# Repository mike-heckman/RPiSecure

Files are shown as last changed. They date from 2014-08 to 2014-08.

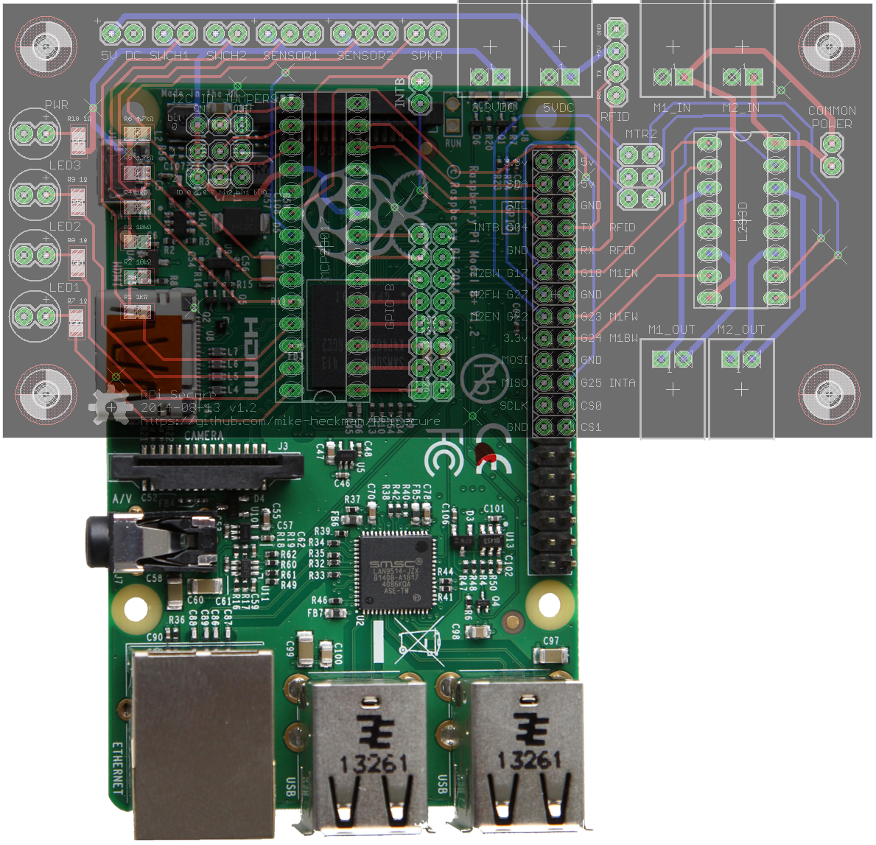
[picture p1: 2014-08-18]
images/Relationship_Pi.png

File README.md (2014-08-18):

Welcome!

This board is designed to "glue" parts to a Raspberry Pi for an RFID door lock.

It attaches on top of the the Pi using the stacking header and uses an L293D
half-H motor driver and an MCP23017 digital IO expander so the other (optional)
components don't take up all the Raspbery Pi's GPIO pins.

If the board is fully populated, it provides the following:

   Two bi-directional motor drivers with either coupled or independent power.
   Connections for two switches, intended for door position (hall-effect sensor) and deadbolt position (tactile momentary switch depressed by the deadbolt).
   Connections for one or two DHT-22 temperature and humidity sensors.
   Connections for up to four LEDs (one is hardwired for power, the other three are on IO ports).
   A connection for a speaker.
   8 additional IO ports addressed through the MCP23017.

The board is designed to use the minimum number of pins on the Raspberry Pi.
To use the second motor driver you have to jumper the MTR2 pins, or tie them
to other pins on the Raspberry Pi breakout.

Also the INTB pins can be jumpered if you want interrupt access to the second
bank of GPIO on the MCP23017 - you don't have to unless you want the interrupt
to go to GPIO pin 4.

You also need to set three jumpers for the MCP23017 3 low id bits.

The board intentionally doesn't draw power from the Pi as it will be powered by
DC/DC power converters from a common 12v source.  There's a pin header near the
upper left corner that provides a +5V and GND power to optionally power the Pi.

The board should work for either the model B or B+ Raspberry Pis.

Datasheets are available for most parts:

L293D Motor Driver:  http://www.farnell.com/datasheets/1804890.pdf
MCP21037 Digital IO: http://www.farnell.com/datasheets/12179.pdf

Standard Traces are 10 mil with 12 mil isolation, the traces for the motor
power in out and to the L293D are larger as it can switch motors up to 36V.
The top and bottom ground planes have been maximized around the chips to allow
them to sink heat into the board.

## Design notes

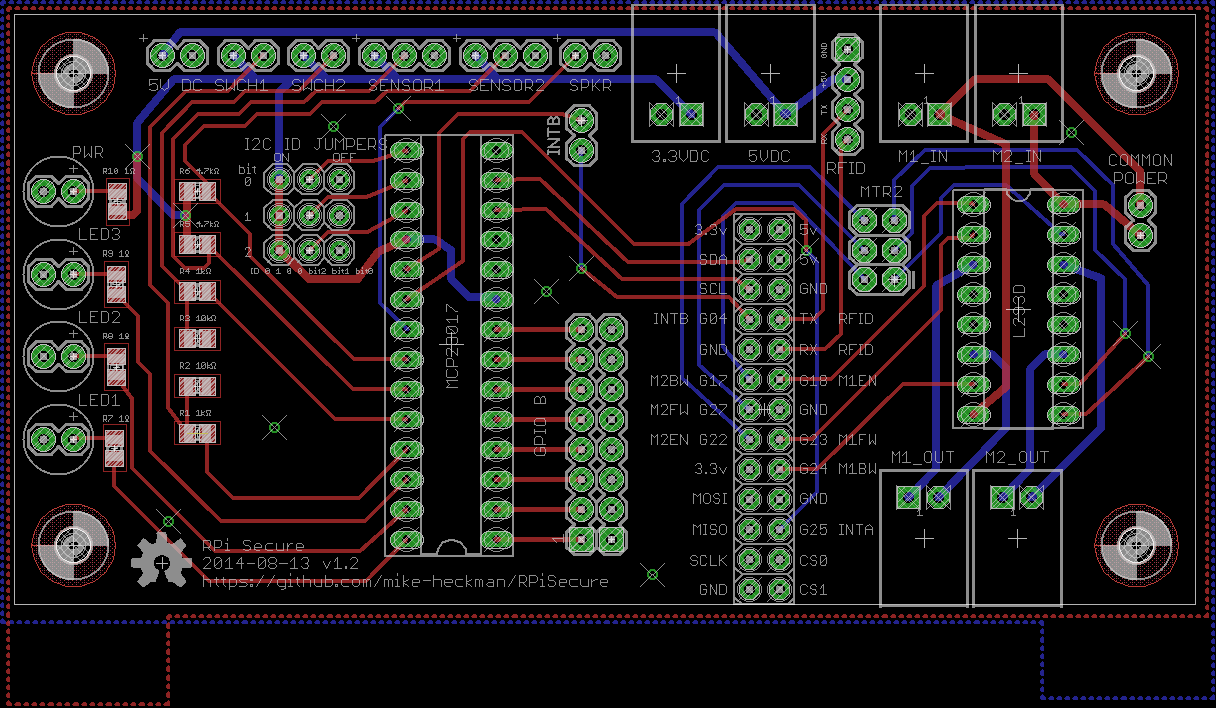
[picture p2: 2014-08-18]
images/RPi_Secure_V1_2.png

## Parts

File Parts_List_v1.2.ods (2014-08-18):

Quantity | Description | Jameco |  | Mouser |  | Adafruit |  | Digikey |  | Newark |  | BEST | Total | Running | Jameco | Mouser | Adafruit | Digikey | Newark | Jameco | Mouser | Adafruit | Digikey | Newark | Total | Order
1 | Industrial & ASIC | link (http://www.jameco.com/webapp/wcs/stores/servlet/Product_10001_10001_1341966_-1) | $2.95 | link (http://www.mouser.com/ProductDetail/Texas-Instruments/L293DNE/?qs=sGAEpiMZZMtYFXwiBRPs0wSafWlCmJbc) | $3.75 | link (http://www.adafruit.com/products/807) | $2.50 | link (http://www.digikey.com/product-search/en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) | $3.75 | link (http://www.newark.com/texas-instruments/l293ne/ic-motor-driver-half-h-1a-dip/dp/06F9524) | $2.24 | $2.24 | $2.24 | $2.24 |  |  |  | $3.75 | $2.24 |  |  |  |  | $2.24 | $2.24 | N01
1 | IC, I/O EXPANDER, 16BIT, 1.7MHZ, DIP-28 |  |  | link (http://www.mouser.com/ProductDetail/Microchip-Technology/MCP23017-E-SP/?qs=sGAEpiMZZMtLck3p7ZBovcWu3APnHHes) | $1.26 | link (http://www.adafruit.com/search?q=MCP23017) | $2.95 | link (http://www.digikey.com/product-detail/en/MCP23017-E/SP/MCP23017-E/SP-ND/894272) | $1.44 | link (http://www.newark.com/microchip/mcp23017-e-sp/ic-i-o-expander-16bit-1-7mhz-dip/dp/31K2959?ost=MCP23017-E/SP) | $1.20 | $1.20 | $1.20 | $3.44 |  |  |  | $1.44 | $1.20 |  |  |  |  | $1.20 | $3.44 | N07
1 | Stacking Header for Raspberry Pi |  |  |  |  | link (http://www.adafruit.com/products/1112) | $1.95 |  |  | link (http://www.newark.com/adafruit-industries/1112/stacking-header-raspberry-pi/dp/53W5726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) | $1.95 | $1.95 | $1.95 | $5.39 |  |  |  |  | $1.95 |  |  |  |  | $1.95 | $5.39 | N09
1 | 16 PIN DIL IC SOCKET (2x8) | link (http://www.jameco.com/webapp/wcs/stores/servlet/Product_10001_10001_37372_-1) | $0.12 | link (http://www.mouser.com/ProductDetail/Microchip-Technology/MCP23017-E-SP/?qs=sGAEpiMZZMtLck3p7ZBovcWu3APnHHes) | $0.10 |  |  | link (http://www.digikey.com/product-detail/en/DILB16P-223TLF/609-4713-ND/4292068) | $0.28 | link (http://www.newark.com/multicomp-formerly-from-spc/spc15498/dip-socket-16pos-through-hole/dp/82K7788) | $0.18 | $0.18 | $0.18 | $5.57 |  |  |  | $0.28 | $0.18 |  |  |  |  | $0.18 | $5.57 | N02
1 | 28 PIN DIL IC SOCKET (2x14) | link (http://www.jameco.com/webapp/wcs/stores/servlet/Product_10001_10001_112272_-1) | $0.25 | link (http://www.mouser.com/ProductDetail/TE-Connectivity-AMP/1-2199298-3/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) | $0.14 |  |  | link (http://www.digikey.com/product-search/en/connectors-interconnects/sockets-for-ics-transistors/1442972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) | $0.47 | link (http://www.newark.com/te-connectivity-amp/1-390261-9/dip-socket-28pos-through-hole/dp/52K3282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) | $0.45 | $0.45 | $0.45 | $6.02 |  |  |  | $0.47 | $0.45 |  |  |  |  | $0.45 | $6.02 | N08
14 | Break-away 0.1" right angle strip male header | link (http://www.jameco.com/webapp/wcs/stores/servlet/Product_10001_10001_690865_-1) | $0.01 | link (http://www.mouser.com/ProductDetail/KOA-Speer/CF1-4CT52A102J/?qs=sGAEpiMZZMu61qfTUdNhGzp6EGxOyudVhjapP1h0W9k=) | $0.07 | link (http://www.adafruit.com/products/1769) | $0.02 | link (http://www.digikey.com/product-detail/en/CF14JT1K00/CF14JT1K00CT-ND/1830350) | $0.05 |  |  | $0.05 | $0.76 | $6.79 |  |  |  | $0.05 |  |  |  |  | $0.76 |  | $6.79 | D02
6 | Right angle board connector |  |  |  |  |  |  | link (http://www.digikey.com/product-search/en?x=0&y=0&lang=en&site=us&keywords=S2B-XH-A(LF)(SN)) | $0.13 | link (http://www.newark.com/jst-japan-solderless-terminals/s2b-xh-a-lf-sn/connector-header-tht-r-a-2-5mm/dp/74M4739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) | $0.29 | $0.13 | $0.79 | $7.58 |  |  |  | $0.13 | $0.29 |  |  |  | $0.79 |  | $7.58 | D01
6 | Crimp end connectors |  |  |  |  |  |  | link (http://www.digikey.com/product-detail/en/SXH-001T-P0.6/455-1135-1-ND/527370) | $0.10 | link (http://www.newark.com/jst-japan-solderless-terminals/bxh-001t-p0-6/contact-crimp-socket-28-22awg/dp/73M9274) | $0.02 | $0.02 | $0.14 | $7.72 |  |  |  | $0.10 | $0.02 |  |  |  |  | $0.14 | $7.72 | N03
6 | Terminal connector |  |  |  |  |  |  | link (http://www.digikey.com/product-detail/en/XHP-2/455-2266-ND/555485) | $0.10 | link (http://www.newark.com/jst-japan-solderless-terminals/xhp-2/wire-to-board-conn-recpt-2pos/dp/72M6922) | $0.05 | $0.05 | $0.28 | $8.00 |  |  |  | $0.10 | $0.05 |  |  |  |  | $0.28 | $8.00 | N04
2 | 0805 SMD 1kΩ Resistor | link (http://www.jameco.com/webapp/wcs/stores/servlet/Product_10001_10001_2078590_-1) | $0.03 | link (http://www.mouser.com/ProductDetail/Vishay-Dale/CRCW08051K00FKEA/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) | $0.05 |  |  | link (http://www.digikey.com/product-detail/en/RNCP0805FTD1K00/RNCP0805FTD1K00CT-ND/2240568) | $0.07 | link (http://www.newark.com/multicomp/mc01w080511k/resistor-1k-0-1w-1-0805/dp/58K4690) | $0.02 | $0.02 | $0.03 | $8.03 |  |  |  | $0.07 | $0.02 |  |  |  |  | $0.03 | $8.03 | N05
2 | 0805 SMD 10kΩ Resistor | link (http://www.jameco.com/webapp/wcs/stores/servlet/Product_10001_10001_1989949_-1) | $0.05 | link (http://www.mouser.com/ProductDetail/Yageo/SR0805JR-0710KL/?qs=sGAEpiMZZMsozux2/wCmWxClxBCY5422) | $0.04 |  |  | link (http://www.digikey.com/product-detail/en/RMCF0805JT10K0/RMCF0805JT10K0CT-ND/1942577) | $0.03 | link (http://www.newark.com/multicomp/mc01w0805110k/resistor-10k-0-1w-1-0805/dp/58K4692) | $0.02 | $0.02 | $0.03 | $8.07 |  |  |  | $0.03 | $0.02 |  |  |  |  | $0.03 | $8.07 | N06
2 | 0805 SMD 4.7kΩ Resistor |  |  |  |  |  |  | link (http://www.digikey.com/product-detail/en/RMCF0805FT4K70/RMCF0805FT4K70CT-ND/1942412) | $0.03 |  |  | $0.03 | $0.06 | $8.13 |  |  |  | $0.03 |  |  |  |  | $0.06 |  | $8.13 | D03
4 | 0805 SMD 1Ω Resistor |  |  |  |  |  |  |  |  | link (http://www.newark.com/vishay-dale/crcw08051r00fnea/resistor-thick-film-chip-1-ohm/dp/52K9792) | $0.01 | $0.01 | $0.02 | $8.15 |  |  |  |  | $0.01 |  |  |  |  | $0.02 | $8.15 | N10
4 | 3.3v LEDs |  | (on hand) |  |  |  |  |  |  |  |  | $0.00 | $0.00 | $8.15 |  |  |  |  |  |  |  |  |  |  | $8.15
47 | Break-away 0.1" straight strip male header |  | (on hand) |  |  |  |  |  |  |  |  | $0.00 | $0.00 | $8.15 |  |  |  |  |  |  |  |  |  |  | $8.15
 |  |  |  |  |  |  |  |  |  |  |  |  |  |  |  |  |  |  |  |  |  |  |  |  | $8.15
 |  |  |  |  |  |  |  |  |  |  |  |  |  |  |  |  |  |  |  |  |  |  |  |  | $8.15
 |  |  |  |  |  |  |  |  |  |  |  |  |  |  |  |  |  |  |  |  |  |  |  |  | $8.15
 |  |  |  |  |  |  |  |  |  |  |  |  |  |  |  |  |  |  |  |  |  |  |  |  | $8.15
 |  |  |  |  |  |  |  |  |  |  |  |  |  |  |  |  |  |  |  |  |  |  |  |  | $8.15
 |  |  |  |  |  |  |  |  |  |  |  |  |  |  |  |  |  |  |  |  |  |  |  |  | $8.15
 |  |  |  |  |  |  |  |  |  |  |  |  |  |  |  |  |  |  |  |  |  |  |  |  | $8.15
 |  |  |  |  |  |  |  |  |  |  |  |  |  |  |  |  |  |  |  |  |  |  |  |  | $8.15
 |  |  |  |  |  |  |  |  |  |  |  |  |  |  |  |  |  |  |  |  |  |  |  |  | $8.15
 |  |  |  |  |  |  |  |  |  |  |  |  |  |  |  |  |  |  |  |  |  |  |  |  | $8.15
 |  |  |  |  |  |  |  |  |  |  |  |  |  |  |  |  |  |  |  |  |  |  |  |  | $8.15
 |  |  |  |  |  |  |  |  |  |  |  |  |  |  |  |  |  |  |  |  |  |  |  |  | $8.15
 |  |  |  |  |  |  |  |  |  |  |  |  |  |  |  |  |  |  |  |  |  |  |  |  | $8.15
 |  |  |  |  |  |  |  |  |  |  |  |  |  |  |  |  |  |  |  |  |  |  |  |  | $8.15
 |  |  |  |  |  |  |  |  |  |  |  |  |  |  |  |  |  |  |  |  |  |  |  |  | $8.15
 |  |  |  |  |  |  |  |  |  |  |  |  |  |  |  |  |  |  |  |  |  |  |  |  | $8.15
 |  |  |  |  |  |  |  |  |  |  |  |  |  |  |  |  |  |  |  |  |  |  |  |  | $8.15
 |  |  |  |  |  |  |  |  |  |  |  |  |  |  |  |  |  |  |  |  |  |  |  |  | $8.15
 |  |  |  |  |  |  |  |  |  |  |  |  |  |  |  |  |  |  |  |  |  |  |  |  | $8.15
 |  |  |  |  |  |  |  |  |  |  |  |  |  |  |  |  |  |  |  |  |  |  |  |  | $8.15
 |  |  |  |  |  |  |  |  |  |  |  |  |  |  |  |  |  |  |  |  |  |  |  |  | $8.15
 |  |  |  |  |  |  |  |  |  |  |  |  |  |  |  |  |  |  |  |  |  |  |  |  | $8.15
 |  |  |  |  |  |  |  |  |  |  |  |  |  |  |  |  |  |  |  |  |  |  |  |  | $8.15
 |  |  |  |  |  |  |  |  |  |  |  |  |  |  |  |  |  |  |  |  |  |  |  |  | $8.15
 |  |  |  |  |  |  |  |  |  |  |  |  |  |  |  |  |  |  |  |  |  |  |  |  | $8.15
 |  |  |  |  |  |  |  |  |  |  |  |  |  |  |  |  |  |  |  |  |  |  |  |  | $8.15
 |  |  |  |  |  |  |  |  |  |  |  |  |  |  |  |  |  |  |  |  |  |  |  |  | $8.15
 |  |  |  |  |  |  |  |  |  |  |  |  |  |  |  |  |  |  |  |  |  |  |  |  | $8.15
 |  |  |  |  |  |  |  |  |  |  |  |  |  |  |  |  |  |  |  |  |  |  |  |  | $8.15
 |  |  |  |  |  |  |  |  |  |  |  |  |  |  |  |  |  |  |  |  |  |  |  |  | $8.15
 |  |  |  |  |  |  |  |  |  |  |  |  |  |  |  |  |  |  |  |  |  |  |  |  | $8.15
 |  |  |  |  |  |  |  |  |  |  |  |  |  |  |  |  |  |  |  |  |  |  |  |  | $8.15
 |  |  |  |  |  |  |  |  |  |  |  |  |  |  |  |  |  |  |  |  |  |  |  |  | $8.15
 |  |  |  |  |  |  |  |  |  |  |  |  |  |  |  |  |  |  |  |  |  |  |  |  | $8.15
 |  |  |  |  |  |  |  |  |  |  |  |  |  |  |  |  |  |  |  |  |  |  |  |  | $8.15
 |  |  |  |  |  |  |  |  |  |  |  |  |  |  |  |  |  |  |  |  |  |  |  |  | $8.15
 |  |  |  |  |  |  |  |  |  |  |  |  |  |  |  |  |  |  |  |  |  |  |  |  | $8.15
 |  |  |  |  |  |  |  |  |  |  |  |  |  |  |  |  |  |  |  |  |  |  |  |  | $8.15
 |  |  |  |  |  |  |  |  |  |  |  |  |  |  |  |  |  |  |  |  |  |  |  |  | $8.15
 |  |  |  |  |  |  |  |  |  |  |  |  |  |  |  |  |  |  |  |  |  |  |  |  | $8.15
 |  |  |  |  |  |  |  |  |  |  |  |  |  |  |  |  |  |  |  |  |  |  |  |  | $8.15
 |  |  |  |  |  |  |  |  |  |  |  |  |  |  |  |  |  |  |  |  |  |  |  |  | $8.15
 |  |  |  |  |  |  |  |  |  |  |  |  |  |  |  |  |  |  |  |  |  |  |  |  | $8.15
 |  |  |  |  |  |  |  |  |  |  |  |  |  |  |  |  |  |  |  |  |  |  |  |  | $8.15
 |  |  |  |  |  |  |  |  |  |  |  |  |  |  |  |  |  |  |  |  |  |  |  |  | $8.15
 |  |  |  |  |  |  |  |  |  |  |  |  |  |  |  |  |  |  |  |  |  |  |  |  | $8.15
 |  |  |  |  |  |  |  |  |  |  |  |  |  |  |  |  |  |  |  |  |  |  |  |  | $8.15
 |  |  |  |  |  |  |  |  |  |  |  |  |  |  |  |  |  |  |  |  |  |  |  |  | $8.15
 |  |  |  |  |  |  |  |  |  |  |  |  |  |  |  |  |  |  |  |  |  |  |  |  | $8.15
 |  |  |  |  |  |  |  |  |  |  |  |  |  |  |  |  |  |  |  |  |  |  |  |  | $8.15
 |  |  |  |  |  |  |  |  |  |  |  |  |  |  |  |  |  |  |  |  |  |  |  |  | $8.15
 |  |  |  |  |  |  |  |  |  |  |  |  |  |  |  |  |  |  |  |  |  |  |  |  | $8.15
 |  |  |  |  |  |  |  |  |  |  |  |  |  |  |  |  |  |  |  |  |  |  |  |  | $8.15
 |  |  |  |  |  |  |  |  |  |  |  |  |  |  |  |  |  |  |  |  |  |  |  |  | $8.15
 |  |  |  |  |  |  |  |  |  |  |  |  |  |  |  |  |  |  |  |  |  |  |  |  | $8.15
 |  |  |  |  |  |  |  |  |  |  |  |  |  |  |  |  |  |  |  |  |  |  |  |  | $8.15
 |  |  |  |  |  |  |  |  |  |  |  |  |  |  |  |  |  |  |  |  |  |  |  |  | $8.15
 |  |  |  |  |  |  |  |  |  |  |  |  |  |  |  |  |  |  |  |  |  |  |  |  | $8.15
 |  |  |  |  |  |  |  |  |  |  |  |  |  |  |  |  |  |  |  |  |  |  |  |  | $8.15
 |  |  |  |  |  |  |  |  |  |  |  |  |  |  |  |  |  |  |  |  |  |  |  |  | $8.15
 |  |  |  |  |  |  |  |  |  |  |  |  |  |  |  |  |  |  |  |  |  |  |  |  | $8.15
 |  |  |  |  |  |  |  |  |  |  |  |  |  |  |  |  |  |  |  |  |  |  |  |  | $8.15
 |  |  |  |  |  |  |  |  |  |  |  |  |  |  |  |  |  |  |  |  |  |  |  |  | $8.15
 |  |  |  |  |  |  |  |  |  |  |  |  |  |  |  |  |  |  |  |  |  |  |  |  | $8.15
 |  |  |  |  |  |  |  |  |  |  |  |  |  |  |  |  |  |  |  |  |  |  |  |  | $8.15
 |  |  |  |  |  |  |  |  |  |  |  |  |  |  |  |  |  |  |  |  |  |  |  |  | $8.15
 |  |  |  |  |  |  |  |  |  |  |  |  |  |  |  |  |  |  |  |  |  |  |  |  | $8.15
 |  |  |  |  |  |  |  |  |  |  |  |  |  |  |  |  |  |  |  |  |  |  |  |  | $8.15
 |  |  |  |  |  |  |  |  |  |  |  |  |  |  |  |  |  |  |  |  |  |  |  |  | $8.15
 |  |  |  |  |  |  |  |  |  |  |  |  |  |  |  |  |  |  |  |  |  |  |  |  | $8.15
 |  |  |  |  |  |  |  |  |  |  |  |  |  |  |  |  |  |  |  |  |  |  |  |  | $8.15
 |  |  |  |  |  |  |  |  |  |  |  |  |  |  |  |  |  |  |  |  |  |  |  |  | $8.15
 |  |  |  |  |  |  |  |  |  |  |  |  |  |  |  |  |  |  |  |  |  |  |  |  | $8.15
 |  |  |  |  |  |  |  |  |  |  |  |  |  |  |  |  |  |  |  |  |  |  |  |  | $8.15
 |  |  |  |  |  |  |  |  |  |  |  |  |  |  |  |  |  |  |  |  |  |  |  |  | $8.15
 |  |  |  |  |  |  |  |  |  |  |  |  |  |  |  |  |  |  |  |  |  |  |  |  | $8.15
 |  |  |  |  |  |  |  |  |  |  |  |  |  |  |  |  |  |  |  |  |  |  |  |  | $8.15
 |  |  |  |  |  |  |  |  |  |  |  |  |  |  |  |  |  |  |  |  |  |  |  |  | $8.15
 |  |  |  |  |  |  |  |  |  |  |  |  |  |  |  |  |  |  |  |  |  |  |  |  | $8.15
 |  |  |  |  |  |  |  |  |  |  |  |  |  |  |  |  |  |  |  |  |  |  |  |  | $8.15
 |  |  |  |  |  |  |  |  |  |  |  |  |  |  |  |  |  |  |  |  |  |  |  |  | $8.15
 |  |  |  |  |  |  |  |  |  |  |  |  |  |  |  |  |  |  |  |  |  |  |  |  | $8.15
 |  |  |  |  |  |  |  |  |  |  |  |  |  |  |  |  |  |  |  |  |  |  |  |  | $8.15
Enabled? |  |  | SubTotal |  | Tax |  | Shipping |  |  |  |  |  | Total | Running
 | Jameco |  |  |  |  |  |  |  |  |  |  |  |  |  | $0.00
 | Mouser |  |  |  |  |  |  |  |  |  |  |  |  |  | $0.00
 | Adafruit |  |  |  |  |  |  |  |  |  |  |  |  |  | $0.00
Y | Digikey |  | $1.61 |  |  |  |  |  |  |  |  |  | $1.61 | $1.61 | $1.61
Y | Newark |  | $6.54 |  |  |  |  |  |  |  |  |  | $6.54 | $8.15 | $8.15
 | TOTAL

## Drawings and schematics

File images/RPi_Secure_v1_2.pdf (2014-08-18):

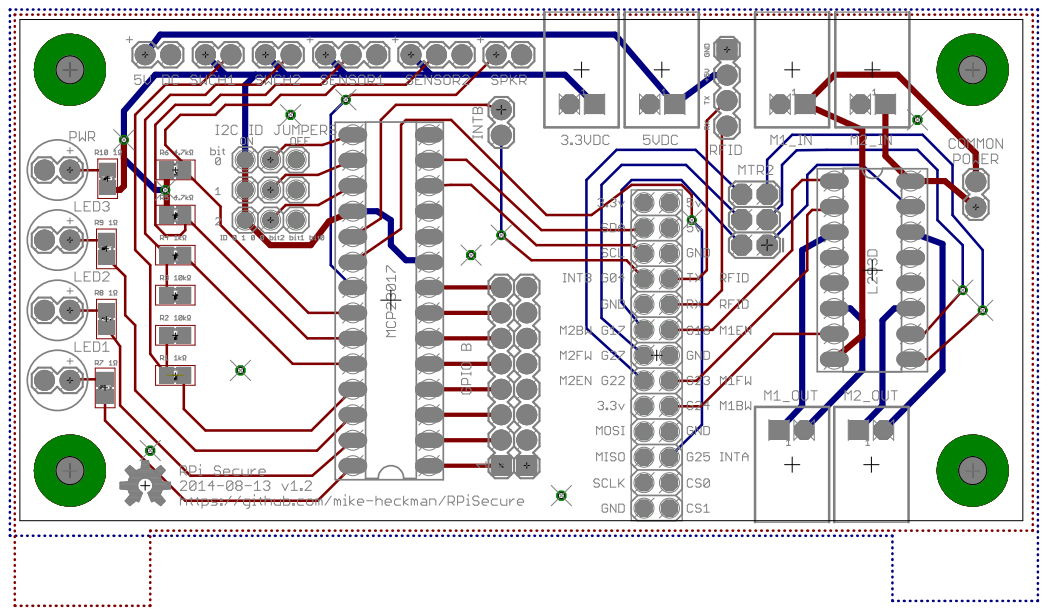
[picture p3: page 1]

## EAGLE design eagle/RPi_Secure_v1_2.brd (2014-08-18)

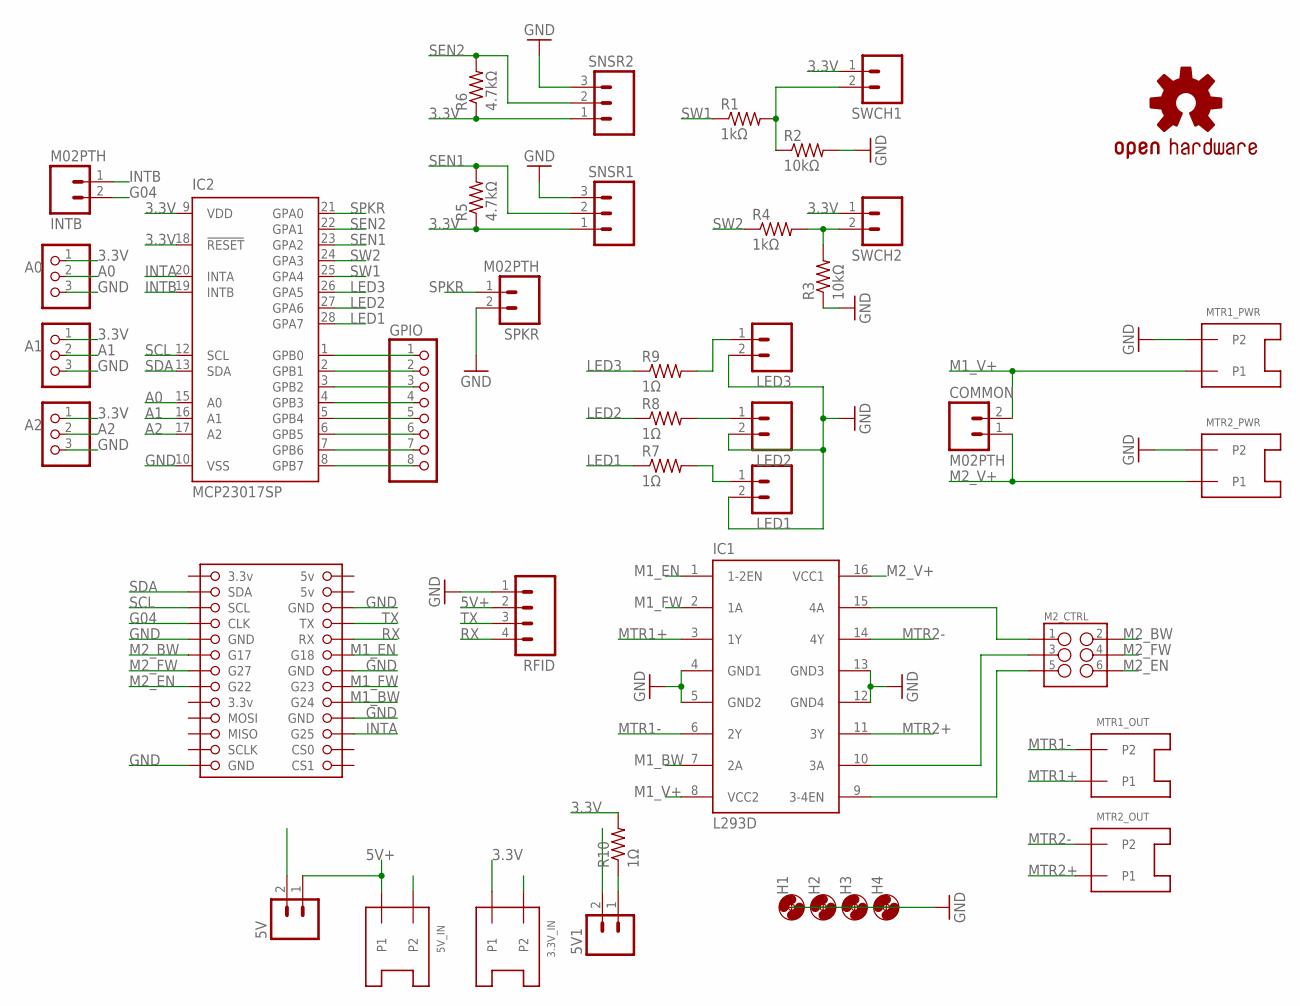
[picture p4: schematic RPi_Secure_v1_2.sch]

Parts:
3.3V_IN, 5V_IN: S2B-XH-AS2B-XH-A; S2B-XH-A
5V, 5V1: M02PTH; 1X02; MPN 22-28-4023
A0, A1, A2: PINHD-1X3; 1X03; MPN 22-28-4033
COMMON: M02PTH; 1X02; MPN 22-28-4023
GPIO: PINHD-1X8; 1X08; MPN 22-28-4080
H1, H2, H3, H4: MOUNT-HOLE2.8; 2,8
IC1: L293D; DIL16
IC2: MCP23017SP; DIL28-3; MPN MCP23017-E/SP
INTB: M02PTH; 1X02; MPN 22-28-4023
JP1: 1112RPI_EXTRA_LONG; 1112
LED1, LED2, LED3: M02PTH; 1X02; MPN 22-28-4023
LOGO2: OSHW-LOGOM; OSHW-LOGO-M
M2_CTRL: M03X22X3_SILK_SM; 2X3
MTR1_OUT, MTR1_PWR, MTR2_OUT, MTR2_PWR: S2B-XH-AS2B-XH-A; S2B-XH-A
R1, R4: 1kΩ; R0805
R2, R3: 10kΩ; R0805
R5, R6: 4.7kΩ; R0805
R7, R8, R9, R10: 1Ω; R0805
RFID: M04PTH; 1X04; MPN 22-28-4040
SNSR1, SNSR2: M03PTH; 1X03; MPN 22-28-4033
SPKR: M02PTH; 1X02; MPN 22-28-4023
SWCH1, SWCH2: M02PTH; 1X02; MPN 22-28-4023

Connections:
01: JP1.01
02: JP1.02
3.3V: 3.3V_IN.P1, A0.1, A1.1, A2.1, IC2.9 (VDD), IC2.18 (!RESET), R5.1, R6.1, R10.2, SNSR1.1, SNSR2.1, SWCH1.1, SWCH2.1
04: JP1.04
5V+: 5V.1, 5V_IN.P1, RFID.2
17: JP1.17
A0: A0.2, IC2.15 (A0)
A1: A1.2, IC2.16 (A1)
A2: A2.2, IC2.17 (A2)
G04: INTB.2, JP1.07
GND: 3.3V_IN.P2, 5V.2, 5V1.2, 5V_IN.P2, A0.3, A1.3, A2.3, IC1.4 (GND1), IC1.5 (GND2), IC1.12 (GND4), IC1.13 (GND3), IC2.10 (VSS), JP1.06, JP1.09, JP1.14, JP1.20, JP1.25, LED1.2, LED2.2, LED3.2, MTR1_PWR.P2, MTR2_PWR.P2, R2.2, R3.1, RFID.1, SNSR1.3, SNSR2.3, SPKR.2
INTA: IC2.20 (INTA), JP1.22
INTB: IC2.19 (INTB), INTB.1
LED1: IC2.28 (GPA7), R7.1
LED2: IC2.27 (GPA6), R8.1
LED3: IC2.26 (GPA5), R9.1
M1_BW: IC1.7 (2A), JP1.18
M1_EN: IC1.1 (1-2EN), JP1.12
M1_FW: IC1.2 (1A), JP1.16
M1_V+: COMMON.2, IC1.8 (VCC2), MTR1_PWR.P1
M2_BW: JP1.11, M2_CTRL.2
M2_EN: JP1.15, M2_CTRL.6
M2_FW: JP1.13, M2_CTRL.4
M2_V+: COMMON.1, IC1.16 (VCC1), MTR2_PWR.P1
MTR1+: IC1.3 (1Y), MTR1_OUT.P1
MTR1-: IC1.6 (2Y), MTR1_OUT.P2
MTR2+: IC1.11 (3Y), MTR2_OUT.P1
MTR2-: IC1.14 (4Y), MTR2_OUT.P2
unnamed: LED1.1, R7.2
unnamed: LED2.1, R8.2
unnamed: LED3.1, R9.2
unnamed: R3.2, R4.2, SWCH2.2
unnamed: 5V1.1, R10.1
unnamed: IC1.10 (3A), M2_CTRL.3
unnamed: IC1.15 (4A), M2_CTRL.1
unnamed: GPIO.1, IC2.1 (GPB0)
unnamed: GPIO.2, IC2.2 (GPB1)
unnamed: GPIO.3, IC2.3 (GPB2)
unnamed: GPIO.4, IC2.4 (GPB3)
unnamed: GPIO.5, IC2.5 (GPB4)
unnamed: GPIO.6, IC2.6 (GPB5)
unnamed: GPIO.7, IC2.7 (GPB6)
unnamed: GPIO.8, IC2.8 (GPB7)
RX: JP1.10, RFID.4
SCL: IC2.12 (SCL), JP1.05
SDA: IC2.13 (SDA), JP1.03
SEN1: IC2.23 (GPA2), R5.2, SNSR1.2
SEN2: IC2.22 (GPA1), R6.2, SNSR2.2
SPKR: IC2.21 (GPA0), SPKR.1
SW1: IC2.25 (GPA4), R1.1, R1.2, R2.1, SWCH1.2
SW2: IC2.24 (GPA3), R4.1
TX: JP1.08, RFID.3
X: IC1.9 (3-4EN), M2_CTRL.5

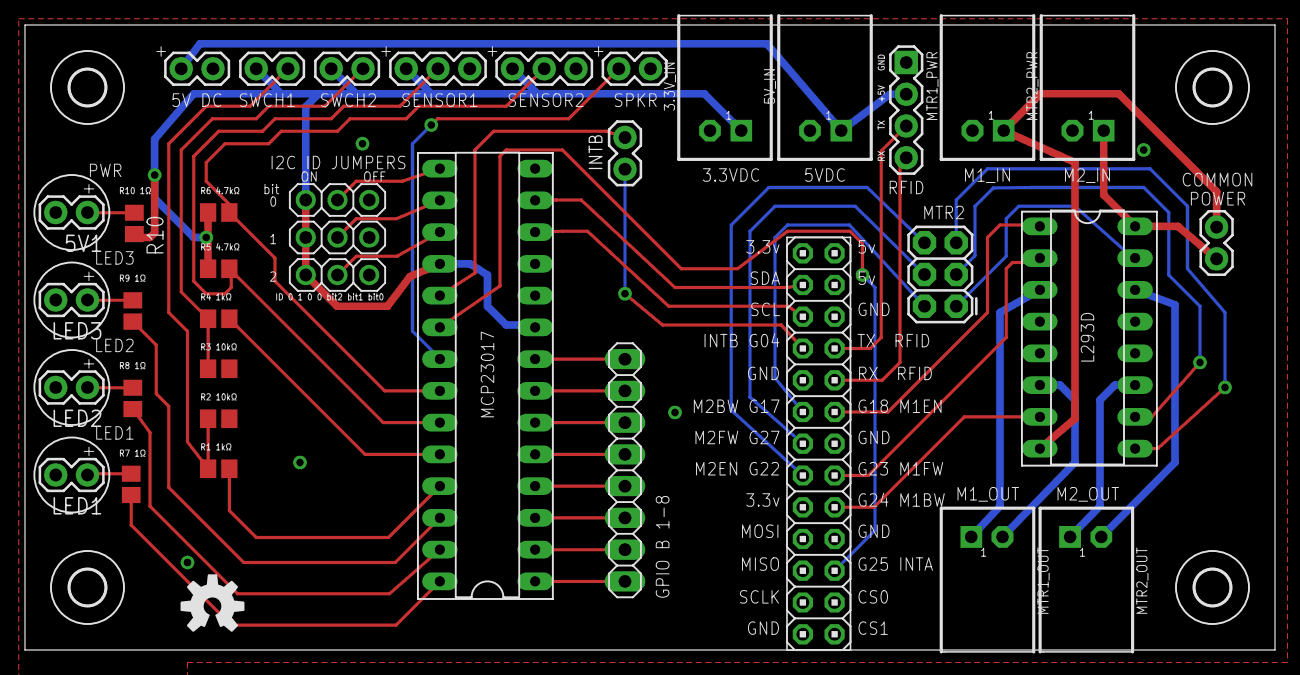
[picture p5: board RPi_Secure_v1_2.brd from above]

Board: 4 copper layers, 100.0 x 50.0 mm, 42 parts (0 on the bottom side), 49 nets.

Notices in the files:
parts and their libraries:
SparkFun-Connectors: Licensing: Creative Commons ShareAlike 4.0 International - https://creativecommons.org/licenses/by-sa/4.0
